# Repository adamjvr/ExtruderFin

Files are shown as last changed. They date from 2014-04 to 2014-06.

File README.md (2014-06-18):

ExtruderFin
===========

A Kinen Fin to add support for 3D printer Extuder and Heated bed to a Kinen compatible TinyG board. This project is a redesign
of the first Kinen fin for temperature control on the kinen platform found here https://github.com/Kinen/TempFin1 . This redesign
transitions the platform away from the Atmel 328p to A FreeScale ARM Cortex M0+ for more performane per dollar. The system wide 
reset is now jumperable so that the fin and the motherboard can be programmed/reset independently of eachother.

To lear more about TinyG and Kinen visit the links below:

https://github.com/synthetos/TinyG
https://github.com/kinen/kinen/wiki

Specs
- FreeScale MKL05Z32VLF4 ARM Cortex M0+ 48MHZ
- Texas Instruments DRV8825 Integrated Stepper Driver
- 3 FDT439N MOSFETs for hotend and two fans
- Maxim Integrated MAX31855EASA+ Thermocouple amplifier
- Two Thermistor channels with shared reference circuit (allows for redundant thermistors instead of a single thermocouple)
- 24VDC System
- ARM Cortex M JTAG port supporting serial wire debugging
- FTDI cable/adapter port for serial firmware loading
- Compatible with the previous Kinen specification and the recently updated specifiation.

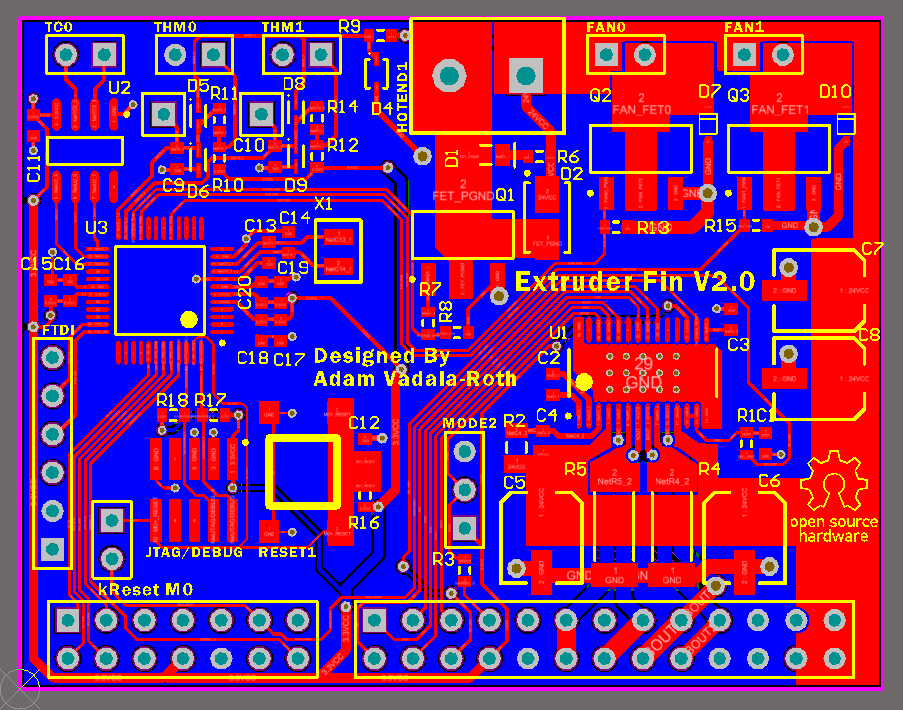
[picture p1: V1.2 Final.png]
Prototype 1


Recently Fabricated Prototype! 6/17/14
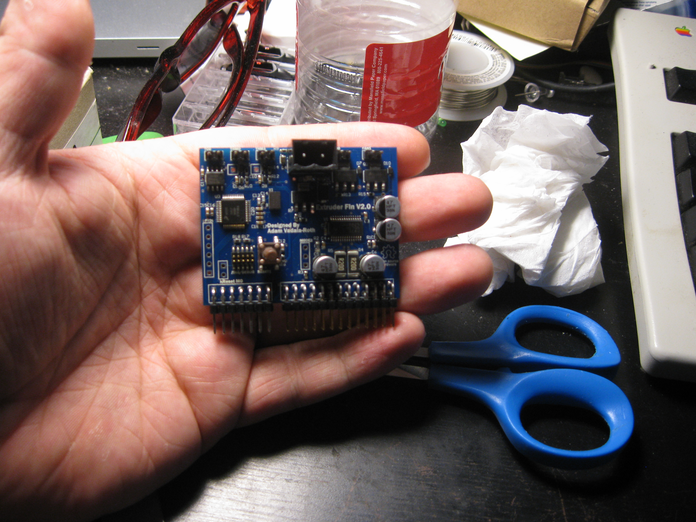
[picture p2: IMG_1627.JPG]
Fabricated Prototype


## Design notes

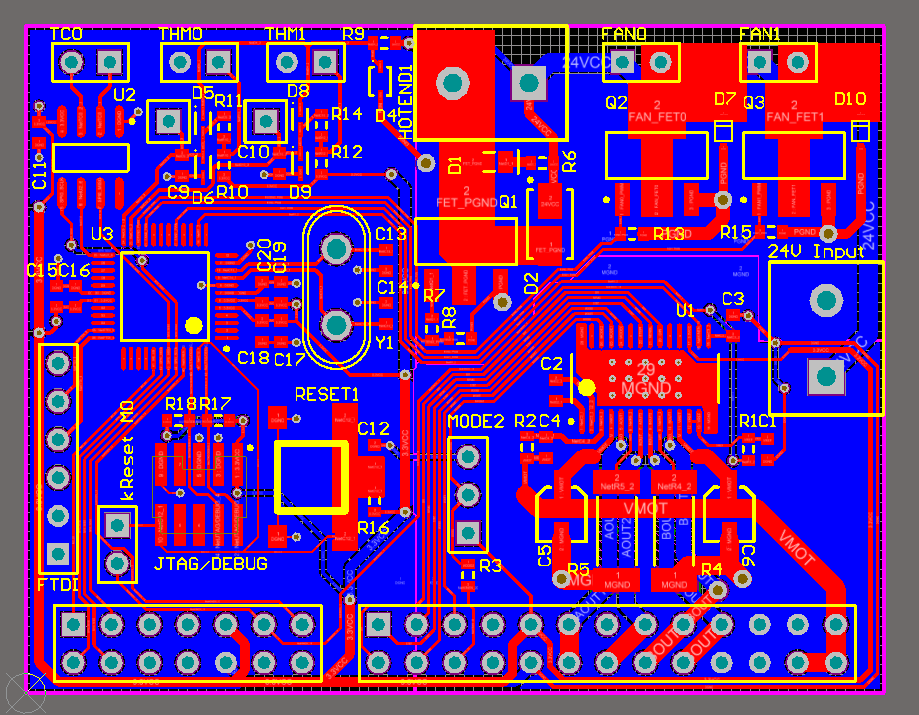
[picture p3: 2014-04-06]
V1.png

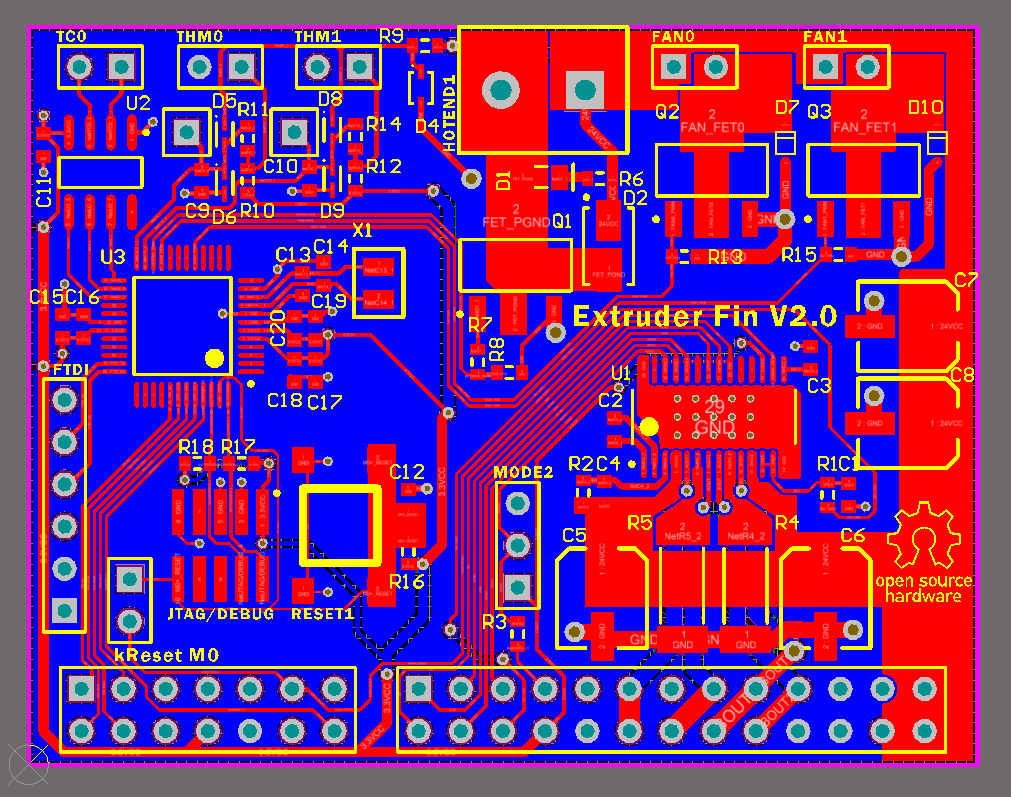
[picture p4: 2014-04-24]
V1.1.png

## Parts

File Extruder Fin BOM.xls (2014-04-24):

Comment | Description | Designator | Footprint | LibRef | Quantity | Value
0603 | Capacitor (Semiconductor SIM Model) | C1 | 1608[0603] | Cap Semi | 1.0 | 0.1uF
0603 | Capacitor (Semiconductor SIM Model) | C2 | 1608[0603] | Cap Semi | 1.0 | 0.01uF 50V
0603 | Capacitor (Semiconductor SIM Model) | C3 | 1608[0603] | Cap Semi | 1.0 | 0.47
0603 | Capacitor (Semiconductor SIM Model) | C4 | 1608[0603] | Cap Semi | 1.0 | 0.1uF 50V
VS C | Polarized Capacitor (Radial) | C5, C6, C7, C8 | Panasonic VS C | Cap Pol1 | 4.0 | 47uF
Cap Semi | Capacitor (Semiconductor SIM Model) | C9, C10, C11 | 1608[0603] | Cap Semi | 3.0 | 100nF
0603 | Capacitor (Semiconductor SIM Model) | C12, C15, C17, C19 | 1608[0603] | Cap Semi | 4.0 | 100nF
0603 | Capacitor (Semiconductor SIM Model) | C13, C14 | 1608[0603] | Cap Semi | 2.0 | 18pF
0603 | Capacitor (Semiconductor SIM Model) | C16, C18, C20 | 1608[0603] | Cap Semi | 3.0 | 1uF
LED1 | Typical RED GaAs LED | D1 | SM 0805 polarized | LED1 | 1.0
B240A-13-F | Schottky Diode | D2 | B240A-13-F | D Schottky | 1.0
SZMM3Z4V7T1G | Zener Diode | D4 | SZMM3Z4V7T1G | D Zener | 1.0
Diode 1N4148 | High Conductance Fast Diode | D5, D6, D8, D9 | 1N4148WT | Diode 1N4148 | 4.0
PMEG1030EH_EJ | Default Diode | D7, D10 | SOD-323 | Diode | 2.0
Header 2 | Header, 2-Pin | FAN0, FAN1, kReset M0, TC0, THM0, THM1 | HDR1X2 | Header 2 | 6.0
Header 6 | Header, 6-Pin | FTDI | HDR1X6 | Header 6 | 1.0
OSTTC02216 |  | HOTEND1 | OSTTC02216 | Pheonix Contact 2X1 | 1.0
ARM Cortex JTAG-DEBUG |  | JTAG/DEBUG | FTSH-105-XX-X-DV | ARM Cortex JTAG-DEBUG Header | 1.0
Kinen Device NEW |  | KINEN | Kinen Port - Device | Kinen Device NEW | 1.0
Header 3 | Header, 3-Pin | MODE2 | HDR1X3 | Header 3 | 1.0
FDT439N | N-Channel MOSFET | Q1, Q2, Q3 | Fairchild FDT439N | Fairchild FDT439N | 3.0
0603 | Resistor | R1 | J1-0603 | Res3 | 1.0 | 2.7K
0603 | Resistor | R2 | J1-0603 | Res3 | 1.0 | 1M
0603 | Resistor | R3 | J1-0603 | Res3 | 1.0 | 0r
2512 | Resistor | R4, R5 | Resistor2512 | Res3 | 2.0 | 0.20
0603 | Resistor | R6 | J1-0603 | Res3 | 1.0 | 1.8K
0603 | Resistor | R7 | J1-0603 | Res3 | 1.0 | 10r
0603 | Resistor | R8, R13, R15 | J1-0603 | Res3 | 3.0 | 100K
Res3 | Resistor | R9 | J1-0603 | Res3 | 1.0 | 10K
Res3 | Resistor | R10, R11, R12, R14 | J1-0603 | Res3 | 4.0 | 4k7
0603 | Resistor | R16, R17, R18 | J1-0603 | Res3 | 3.0 | 1K
Tactile Switch |  | RESET1 | Mountain Switch TS6324T1607 | Tactile Switch | 1.0
TP4 | Socket | THM_TP1, THM_TP2 | PIN1 | Socket | 2.0
DRV8825 | DRV8825 Ti Stepper Driver | U1 | DRV8825 | DRV8825 | 1.0
MAX31855EASA+ | Cold Junction Compensated Thermocouple to Digital Converter, 14 Bits Temperature Resolution, -40 to 125 degC, 8-Pin SOIC (S8+4), Pb-Free | U2 | MAXM-S8+4_N | MAX31855EASA+ | 1.0
MKL05Z32VLF4 | ARM Cortex M0+ | U3 | MKL05Z32VLF4 | MKL05Z32VLF4 | 1.0
ABS07-32.768KHZ-T | ABS07-32.768KHZ-T RTC Crystal Oscillator | X1 | ABS07-32.768KHZ-T | ABS07-32.768KHZ-T | 1.0

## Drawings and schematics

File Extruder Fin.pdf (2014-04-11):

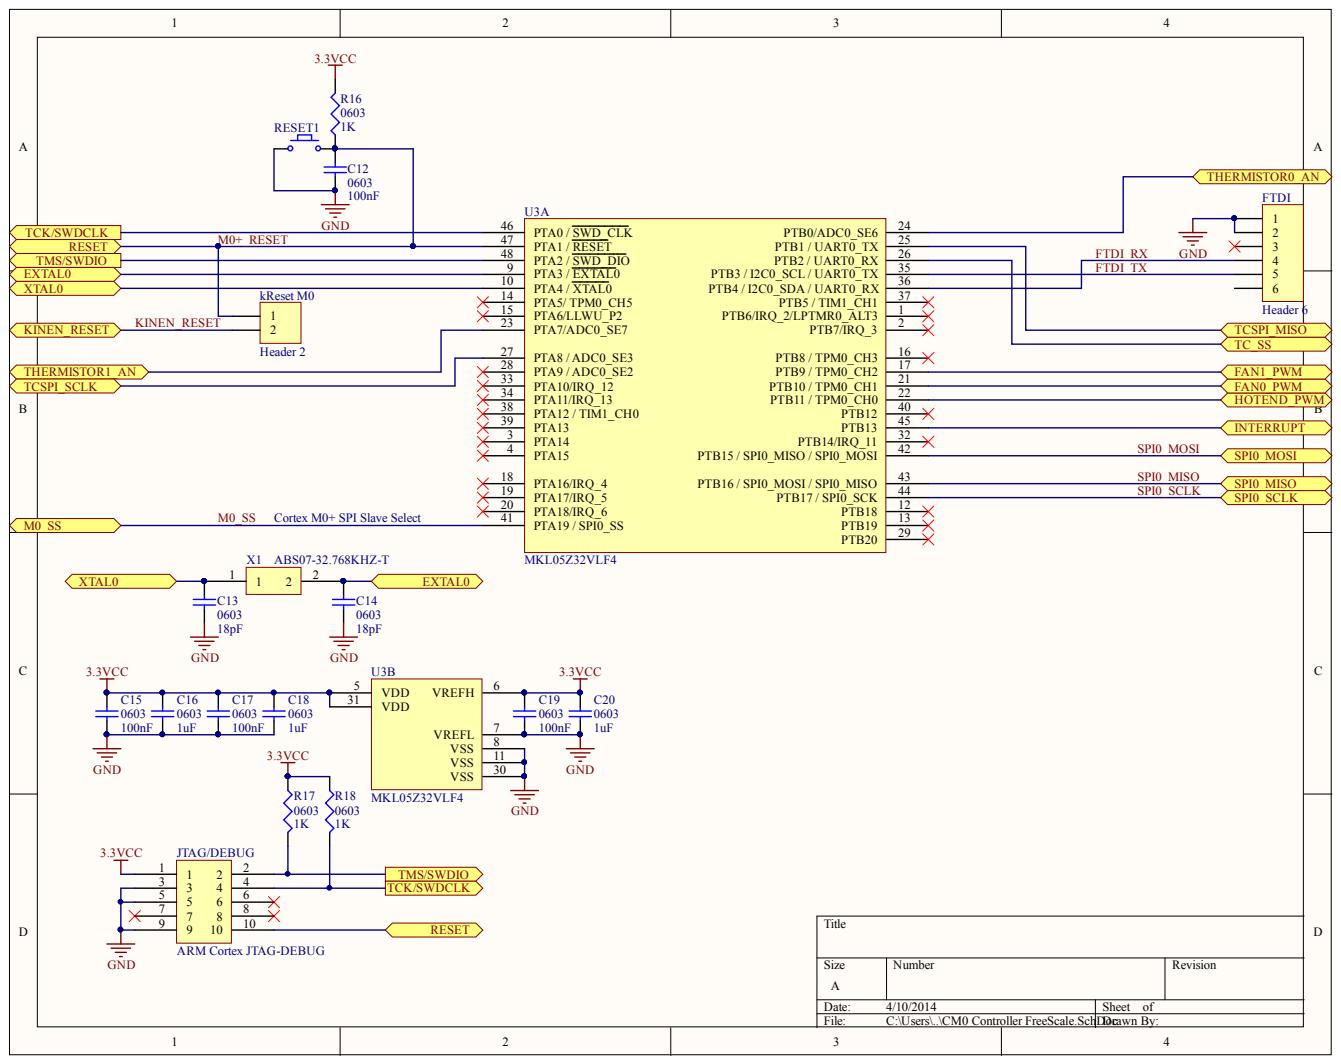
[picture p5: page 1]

Cortex M0+ SPI Slave Select

ARM Cortex JTAG-DEBUG

Date: 4/10/2014 | Sheet of
File: C:\Users\..\CM0 Controller FreeScale.SchDDocrawn By:

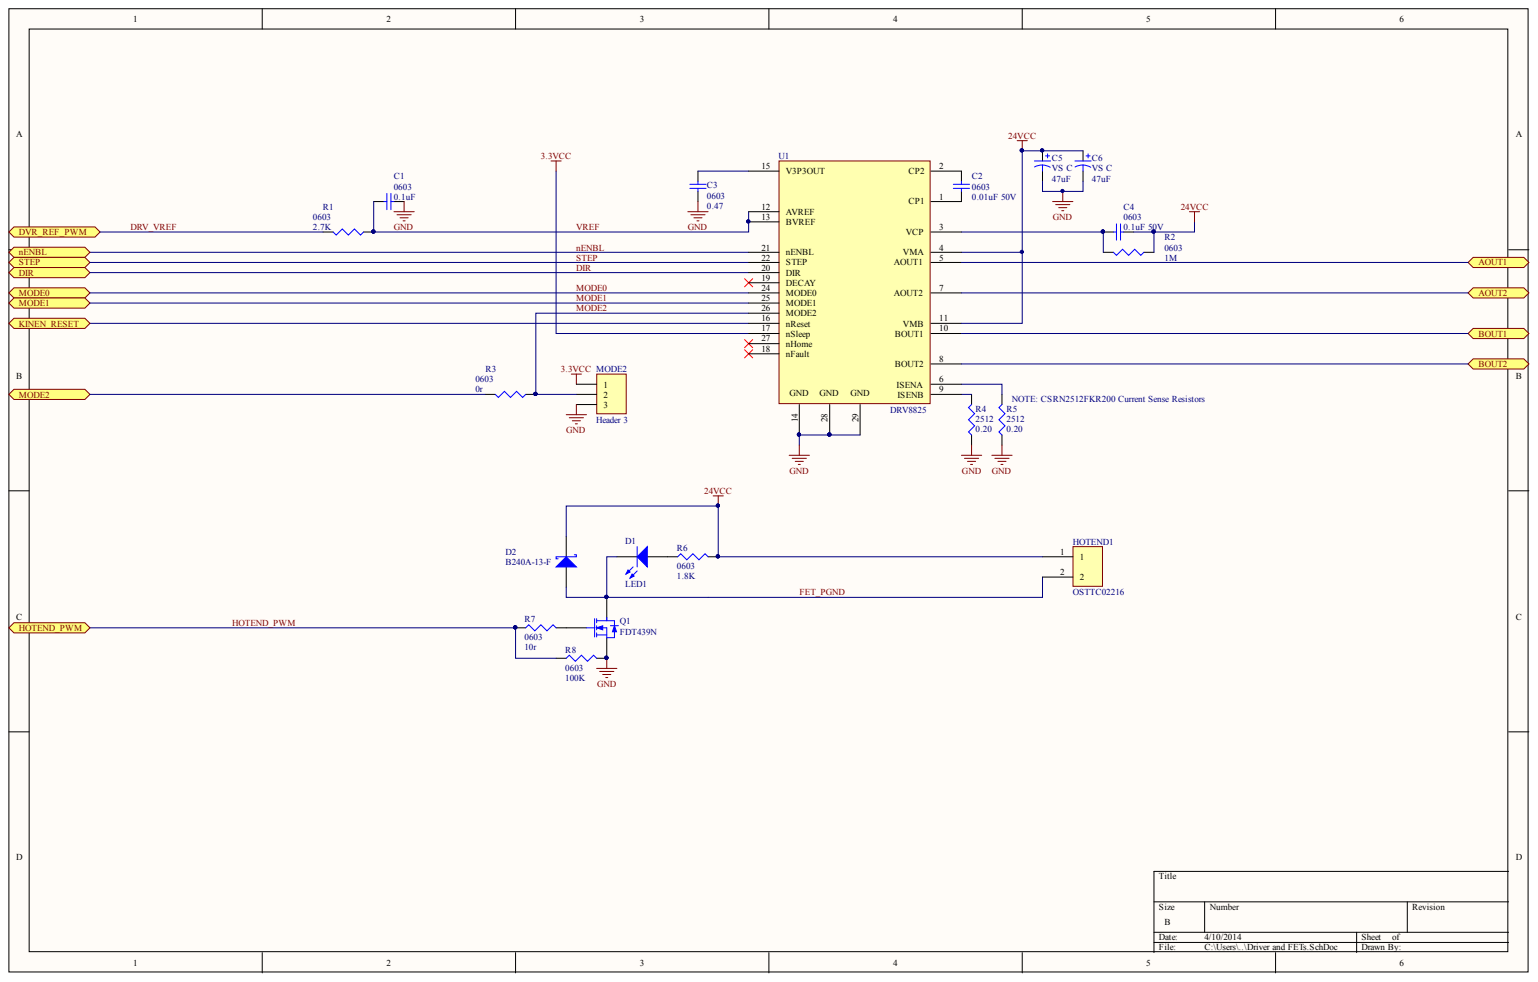
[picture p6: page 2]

S i z e | Numbe r | R evi s ion

e : 4/10/2014 | She et of
F i l e : C : \ U s er s \ . . \ D rive r and F E Ts . S chDoc | D rawn By:

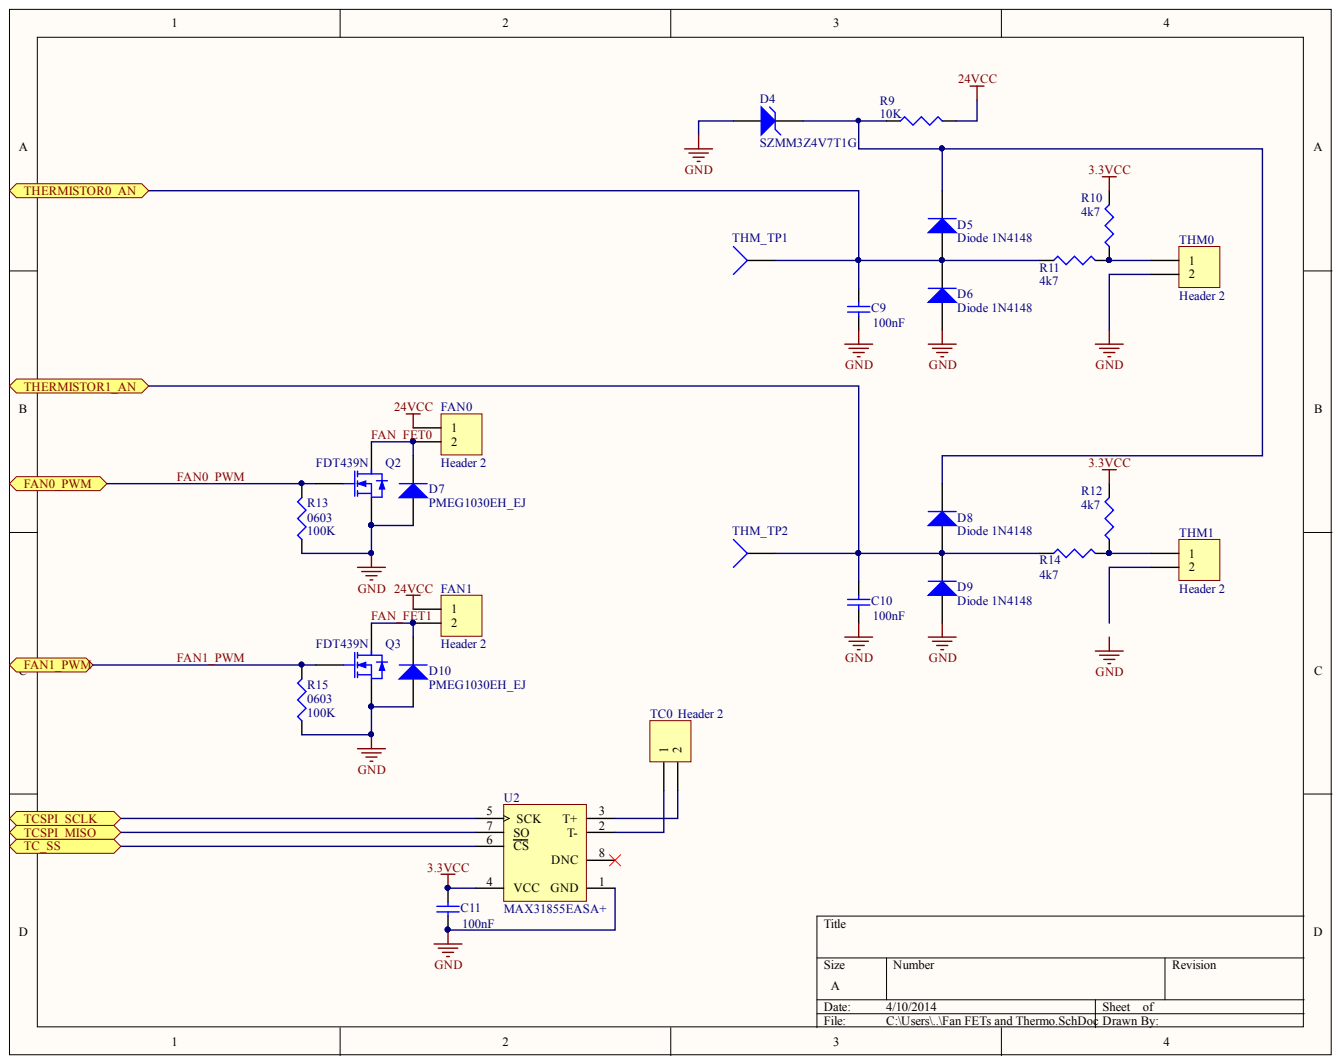
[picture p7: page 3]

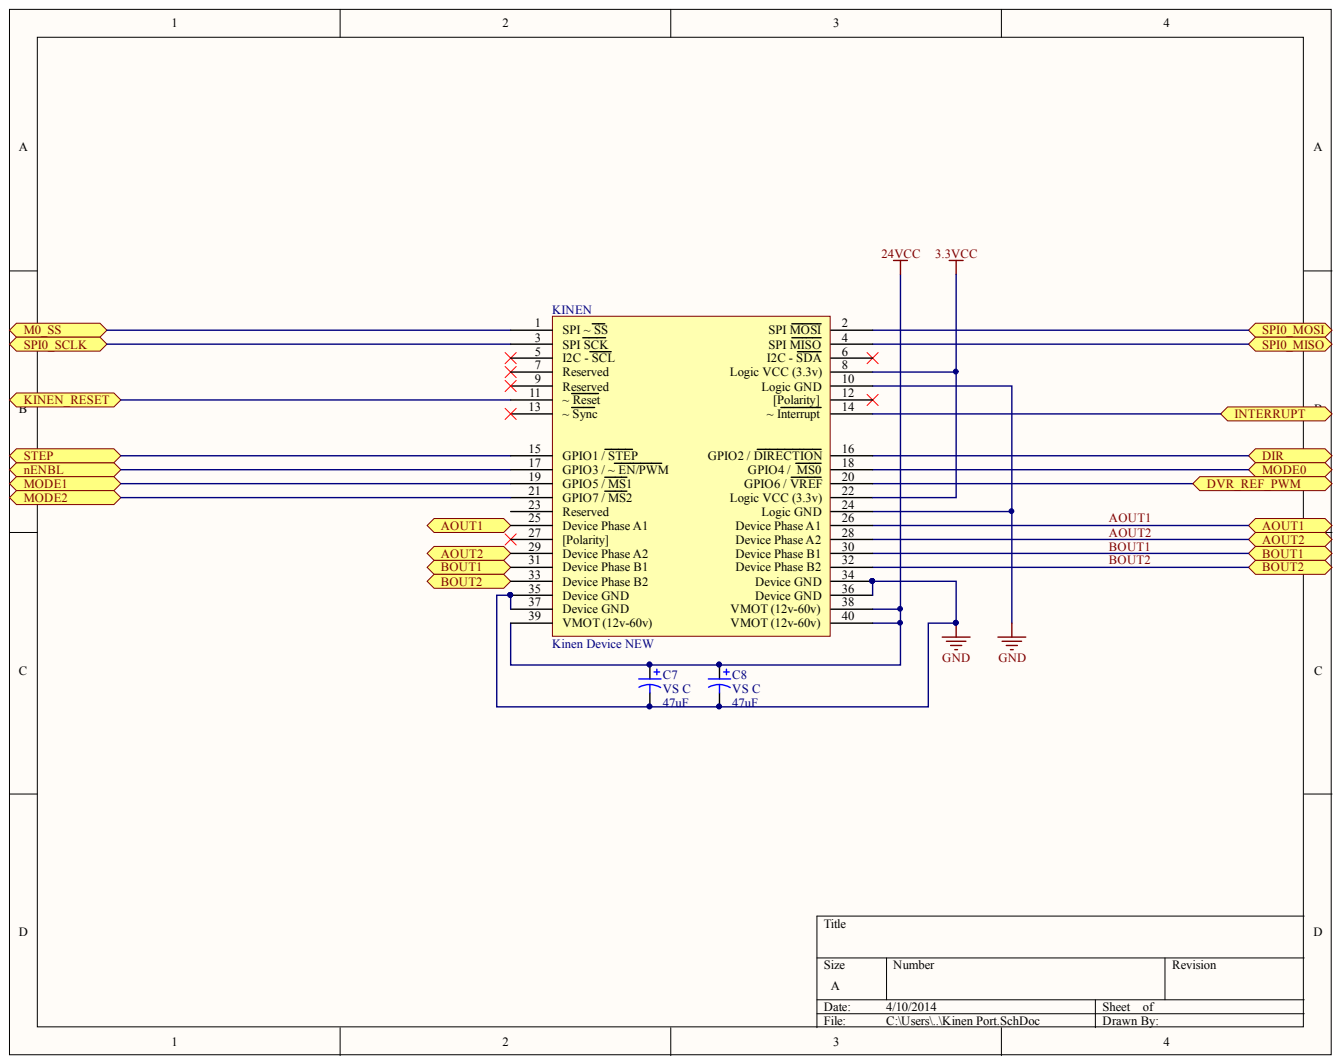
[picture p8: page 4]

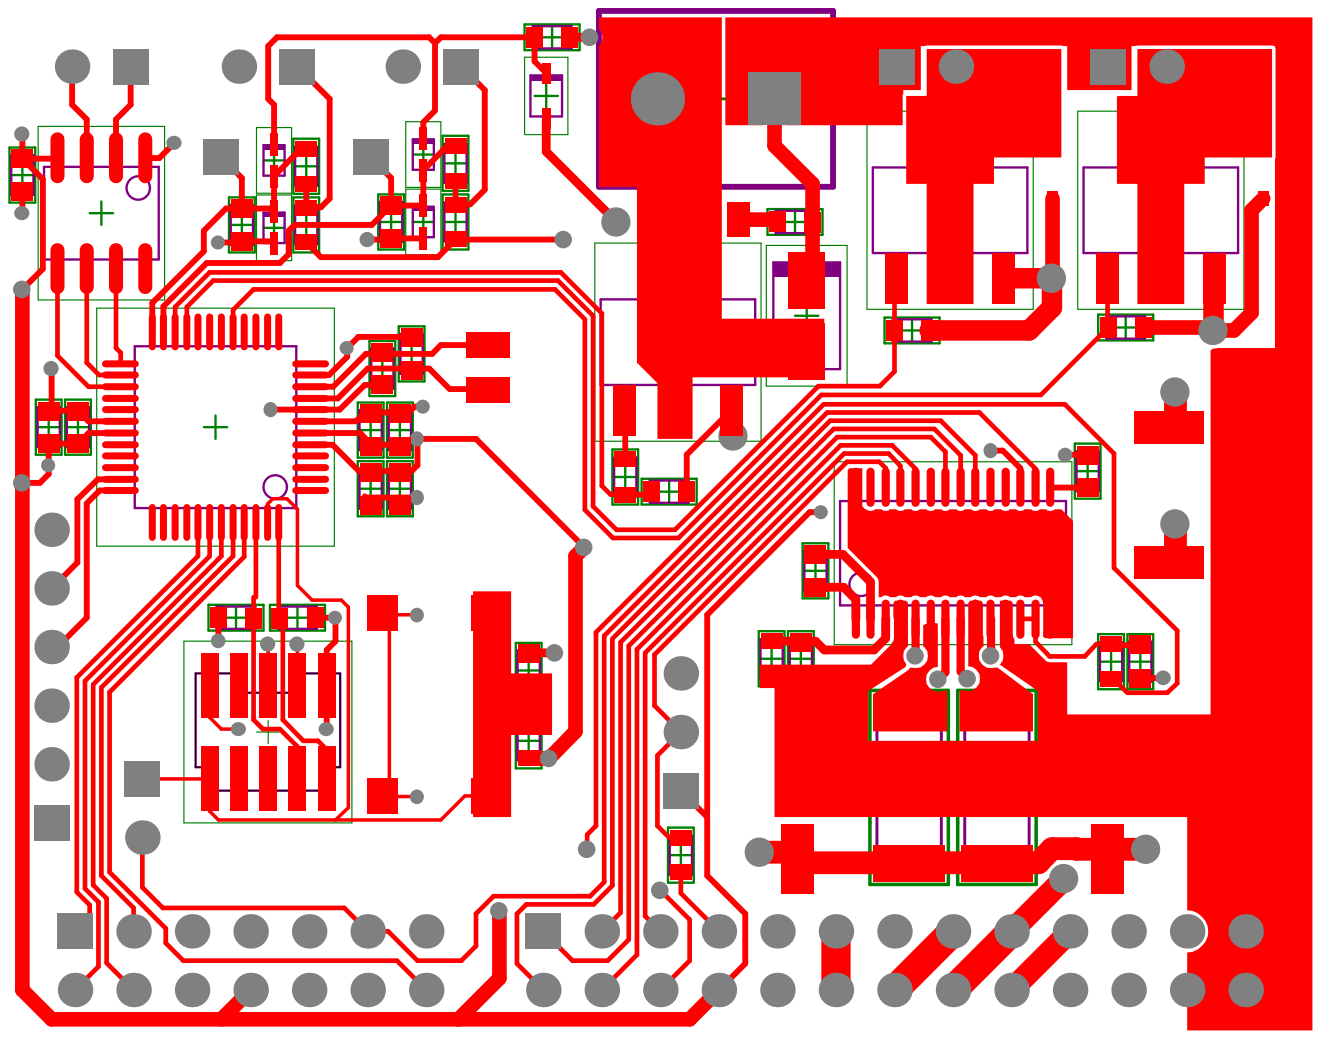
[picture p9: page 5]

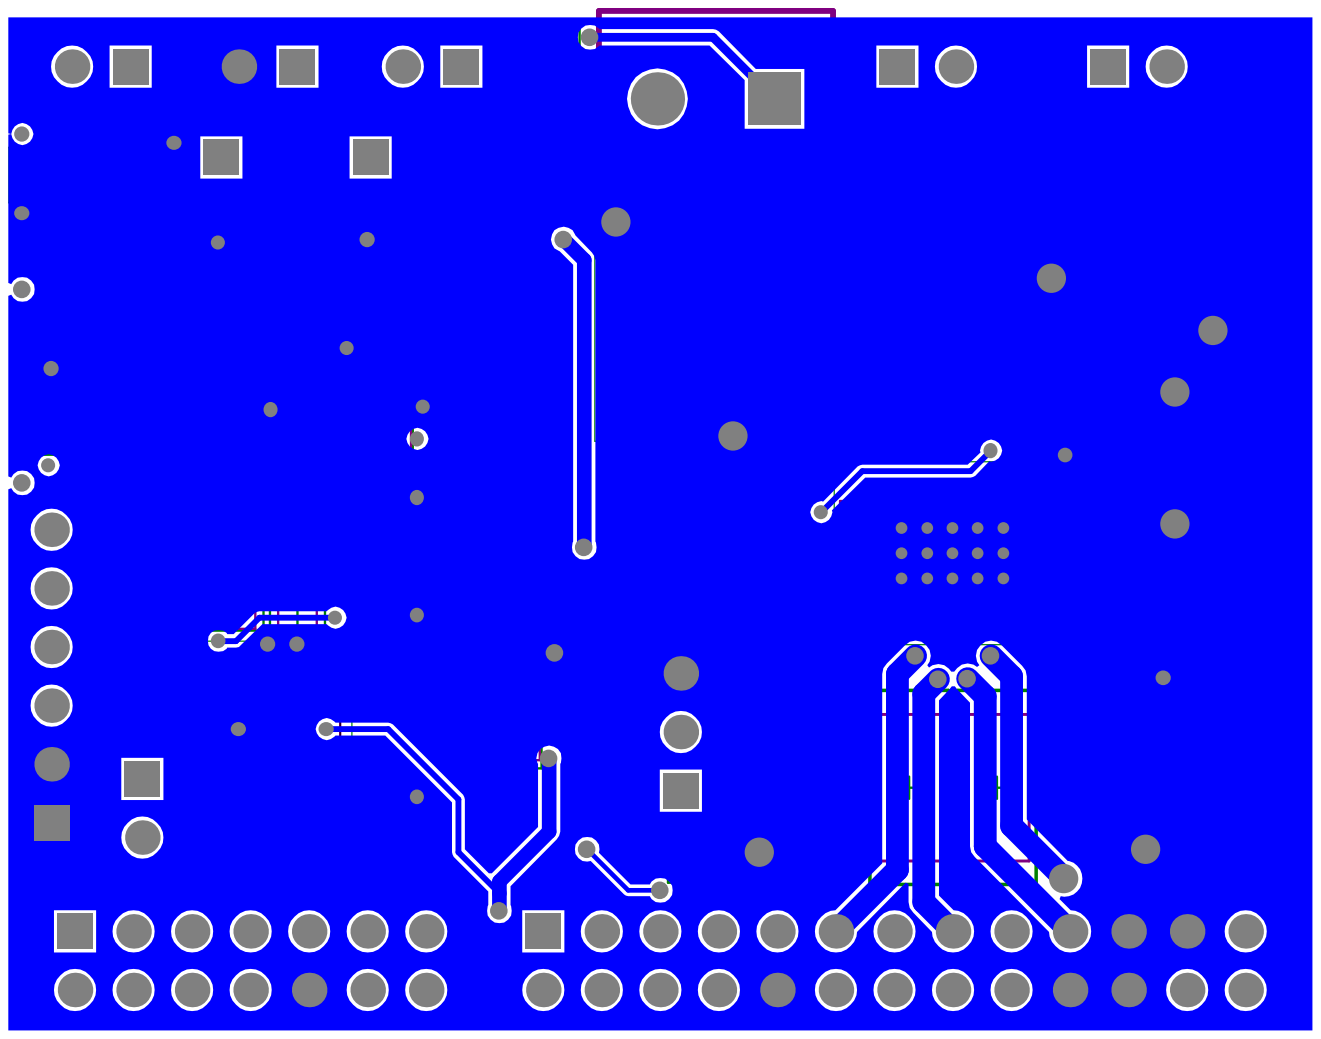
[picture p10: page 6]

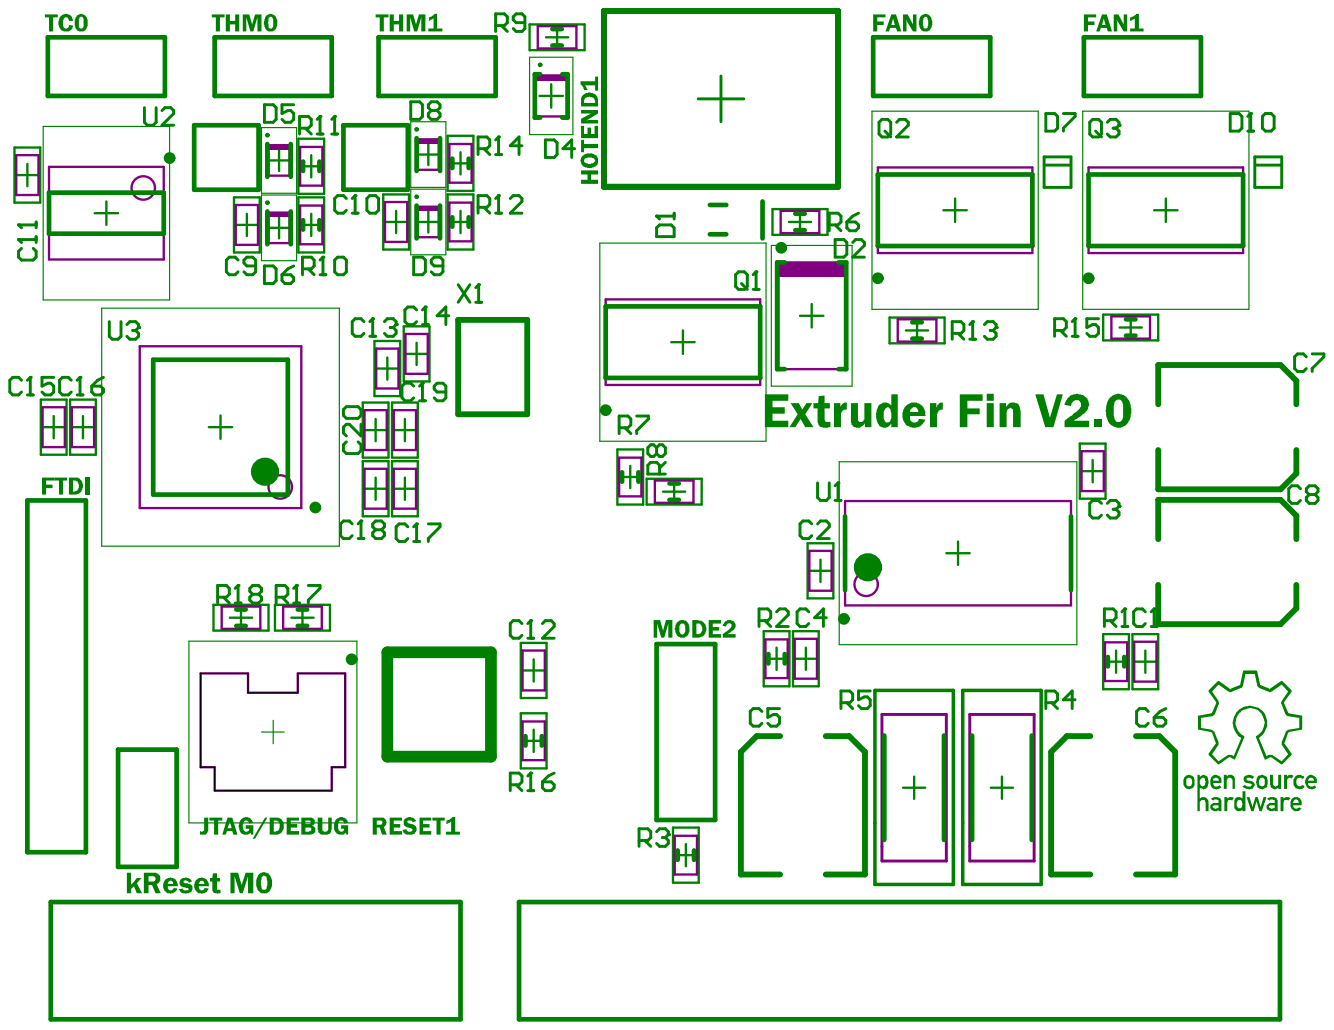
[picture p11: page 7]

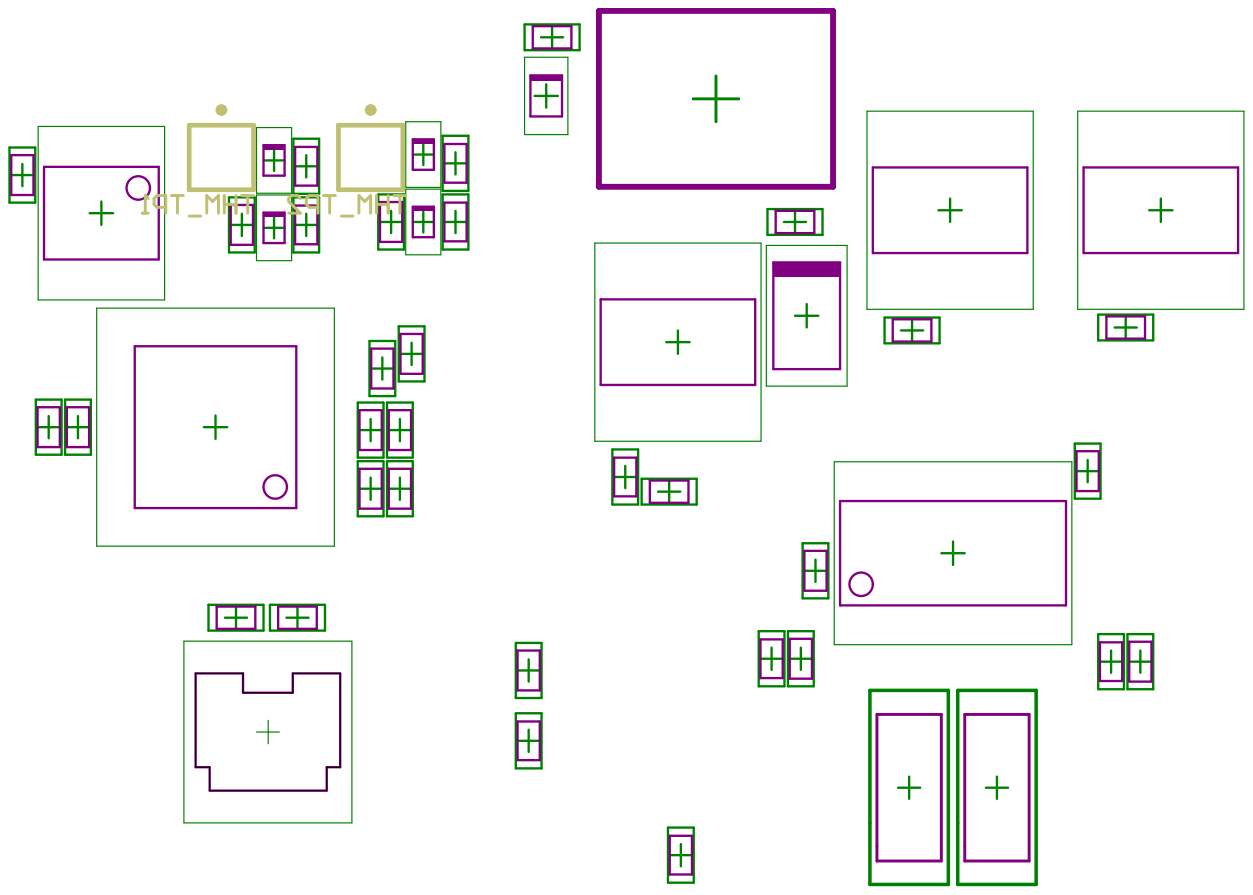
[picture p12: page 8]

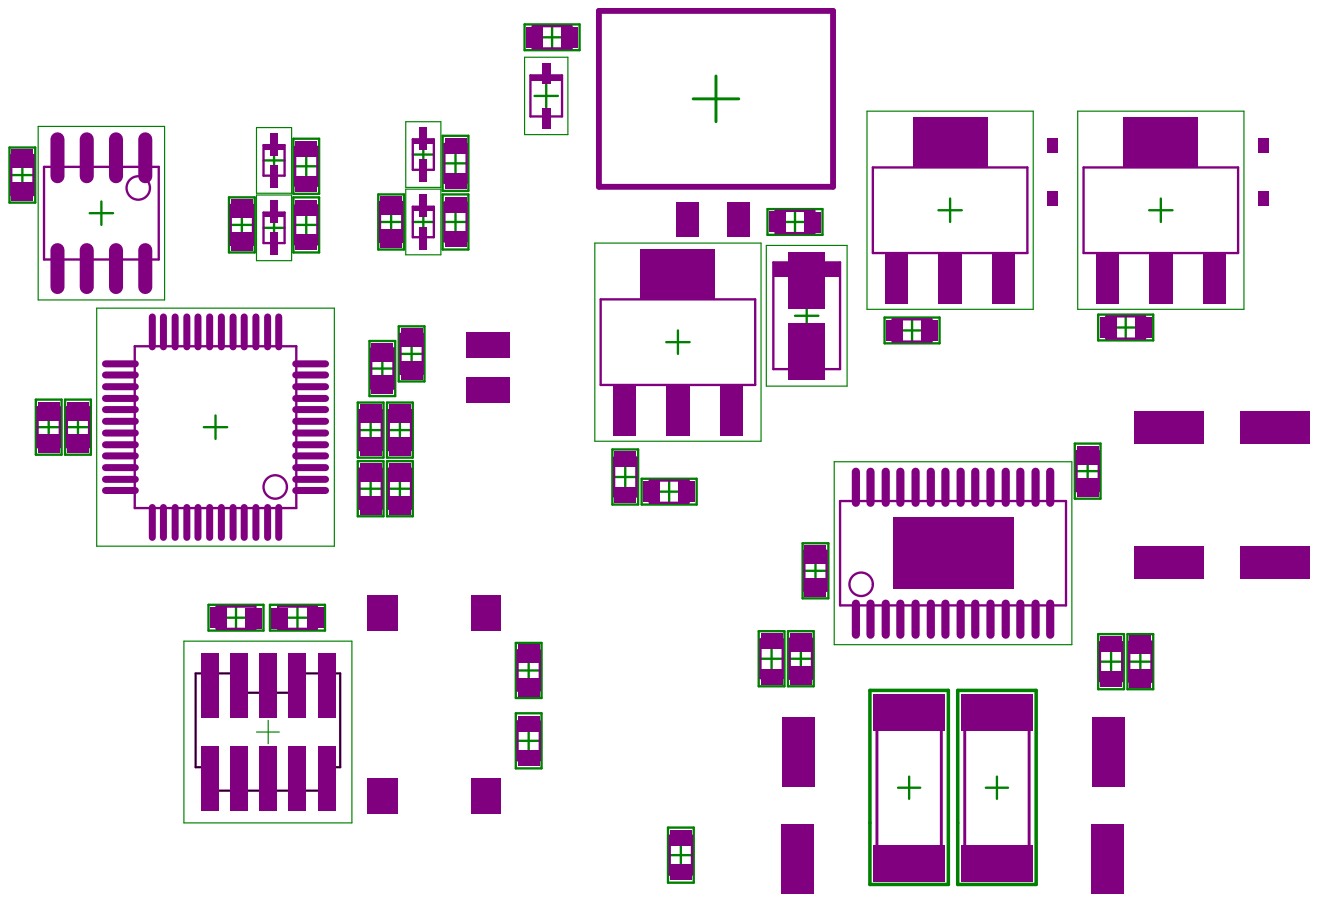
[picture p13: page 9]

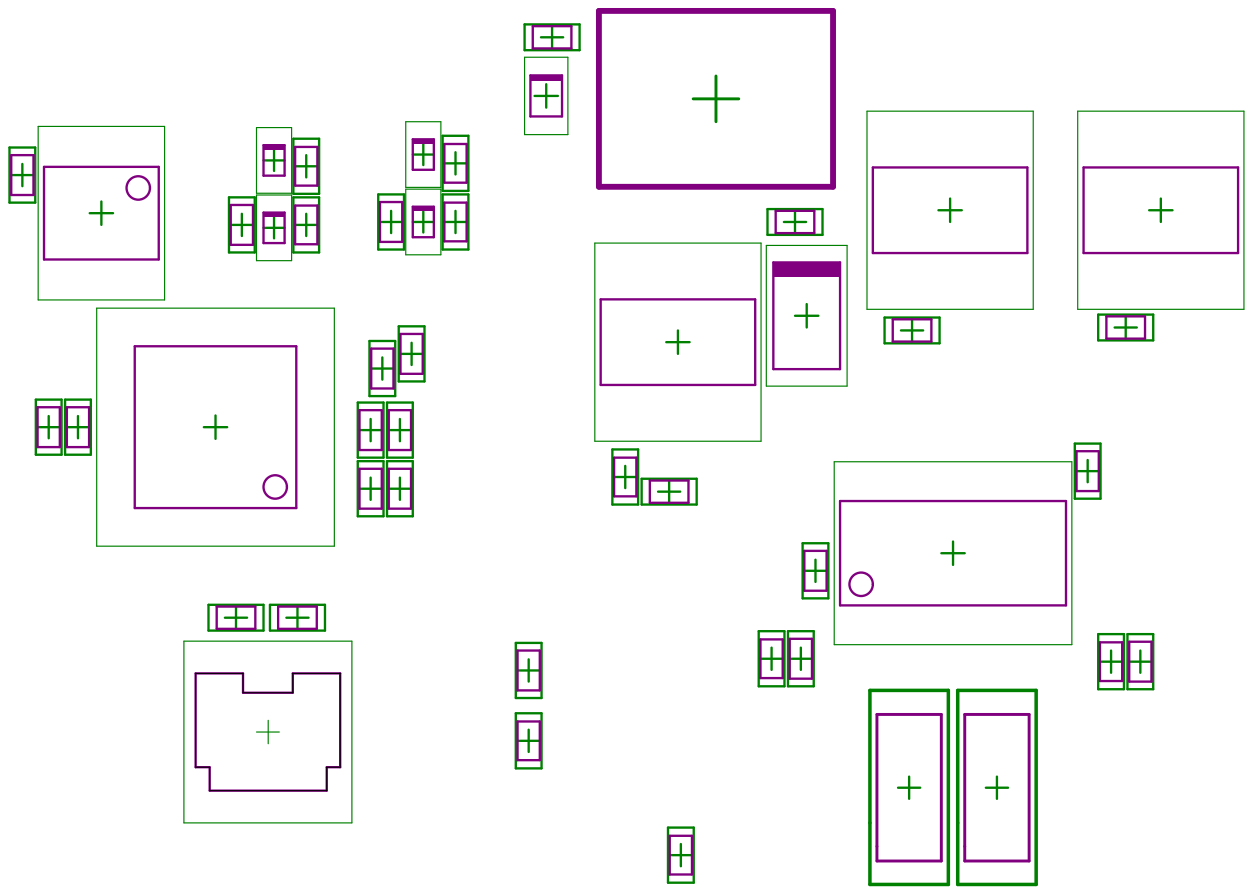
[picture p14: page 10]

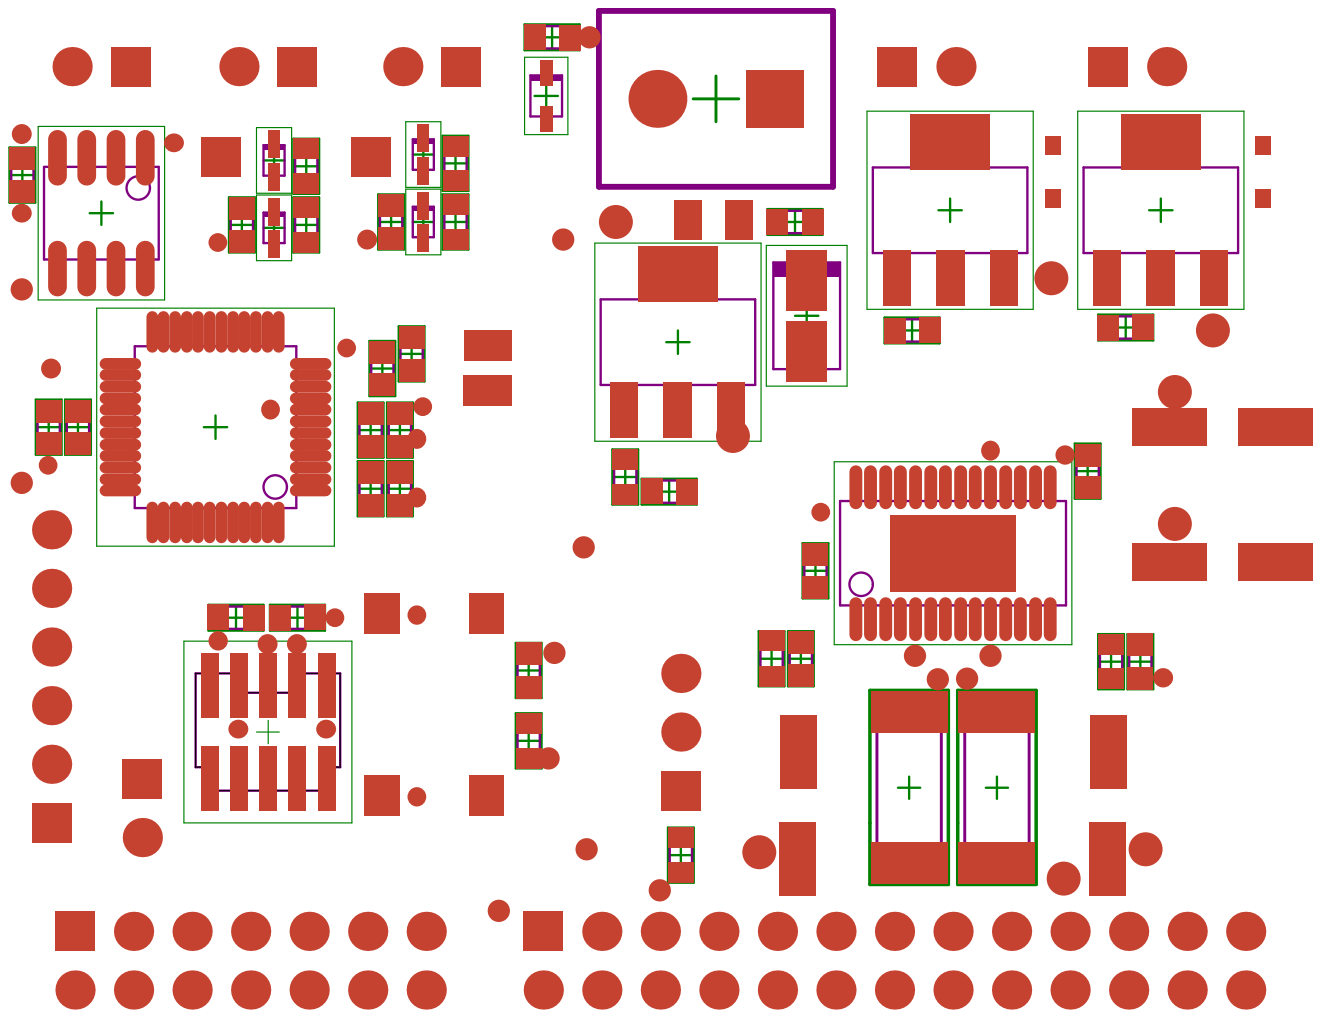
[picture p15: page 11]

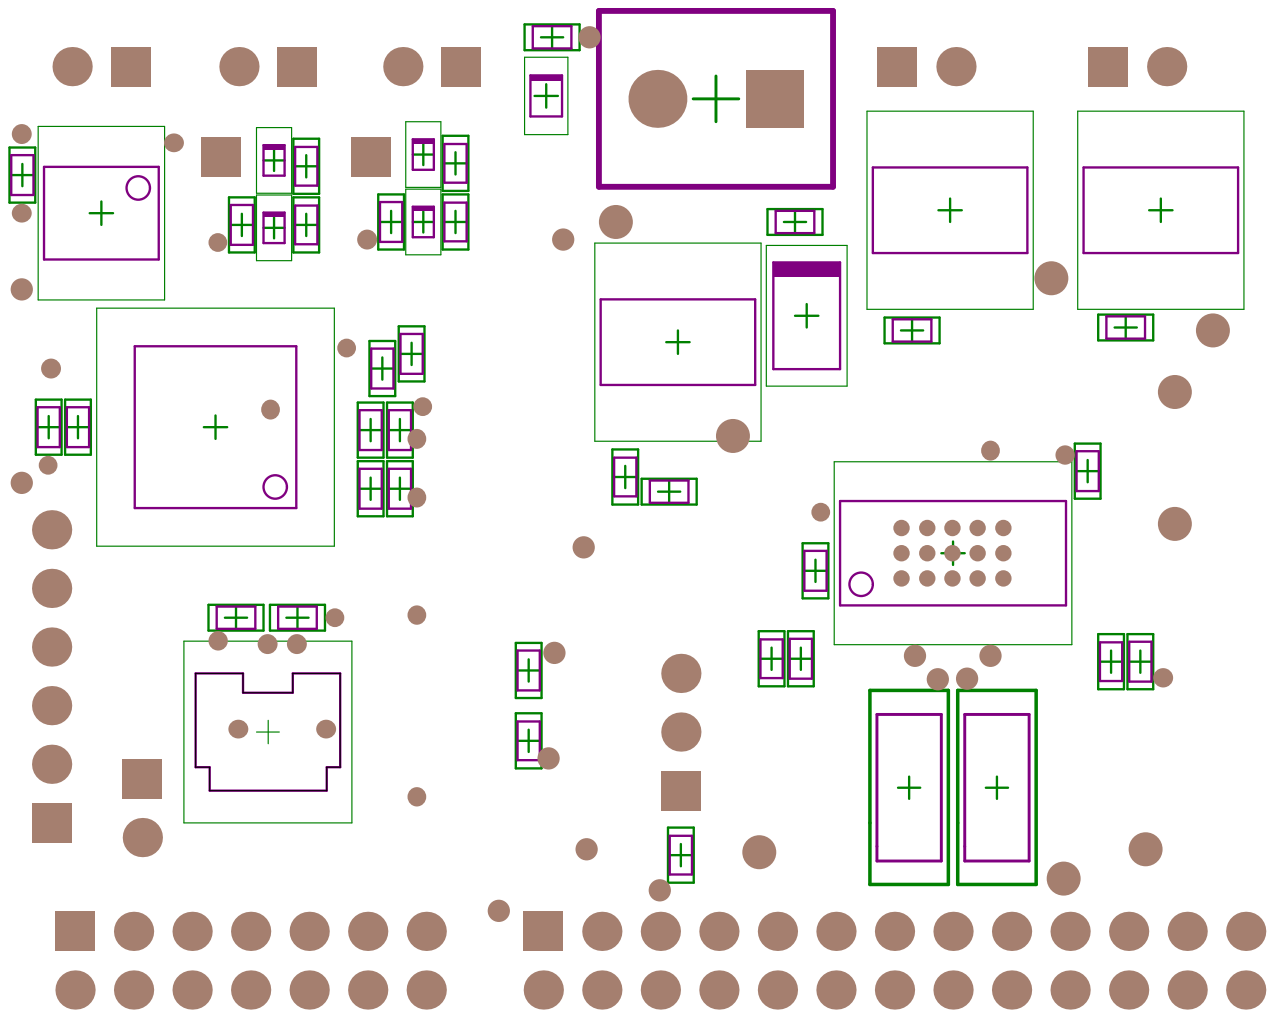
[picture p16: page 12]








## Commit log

2014-03-28 Initial Commit
    Pushing first day of work
    [CM0 Controller.SchDoc, Driver and FETs.SchDoc, Extruder Fin System.SchDoc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]
2014-03-29 Updates
    Schematic 95% complete, changes from my ideas to Aldens implemented.
    Waiting on updates for the kinen spec.
    [CM0 Controller.SchDoc, Driver and FETs.SchDoc, Extruder Fin System.SchDoc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]
2014-03-30 Change from ST to FreeScale
    Switched from the STM32F030C6T6 to the FreeScale KL05P48M4SF1. The
    DRV8825 schematic was updated with Alden's updates.
    [CM0 Controller FreeScale.SchDoc, CM0 Controller STM32F030C6T6.SchDoc, CM0 Controller.SchDoc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]
2014-04-04 Schematic Complete
    Schematic is complete, board layout started.
    [CM0 Controller FreeScale.SchDoc, Driver and FETs.SchDoc, Extruder Fin System.SchDoc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]
2014-04-06 PCB Done
    PCB rev 1 complete, conference with Alden tomorrow.
    Clamping Diodes? Ask Johnny.
    [CM0 Controller FreeScale.SchDoc, Driver and FETs.SchDoc, Extruder Fin.PcbDoc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]
2014-04-07 PCB Updated
    PCB changed as per discussion with Alden. Changed to unified ground
    plane and routed 24v rail as a polygon on the top layer. 24v rail
    decoupling added and cap size increased on DRV8825 decoupling.
    [CM0 Controller FreeScale.SchDoc, Driver and FETs.SchDoc, Extruder Fin.PcbDoc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]
2014-04-11 Changes and Update
    Updated with changes requested by Alden. Kinen reset removed and
    replaced with Kinen interrupt, same GPIO on the M0+. Improved traces for
    current sensing resistors. Changed crystal footprint and traces. Updated
    kinen connector schematic symbol. Changed 3.3v to run of IOREF.
    [CM0 Controller FreeScale.SchDoc, Driver and FETs.SchDoc, Extruder Fin.PcbDoc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]
2014-04-11 Crystal Changed
    Crystal changed to a small form-factor package from Abracom
    [CM0 Controller FreeScale.SchDoc, Extruder Fin.PcbDoc]
2014-04-24 Final
    Finalized and ready for fab
    [CM0 Controller FreeScale.SchDoc, Driver and FETs.SchDoc, Extruder Fin BOM.xls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]
2014-06-18 Picture
    prototype picture added.
